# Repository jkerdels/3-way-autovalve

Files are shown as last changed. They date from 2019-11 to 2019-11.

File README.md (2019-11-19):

# 3-way-autovalve
A motorized 3-way-valve to automatically supply washing machines with warm or cold water to reduce the electricity needed by the washing machine.

This project contains all the necessary files to build a motorized 3-way-valve that can supply a washing machine with first warm and then cold water during a regular washing program in order to reduce the overall electric energy needed by the washing machine.

The design is based on some underlying constraints:

- no modification of the particular washing machine
- all custom mechanical parts should be printable with a low-end 3D-printer
- parts should be easily repairable
- if something breaks, it should still be possible to operate the valve manually
- all parts used should be off-the-shelf, cheap, and easy to acquire
- programming is done using the arduino platform to keep things simple

As sole sensor the device uses a flow meter to measure the volume of water that is supplied to the washing at multiple points in time during the washing program. Based on that the code running on the arduino estimates at which stage of a typical washing program (main phase + multiple rinses) the washing machine is. It supplies warm water for the main phase and cold water for all other phases, and resets automatically when the washing program has reached its end.

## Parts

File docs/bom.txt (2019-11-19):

Bill of materials for this project (a.k.a. the stuff you need):

2x
ball valve with 1/2" threads
example: https://www.amazon.de/gp/product/B00NVGNDTA/ref=ppx_yo_dt_b_asin_title_o03_s00

1x
T-connector with 1/2" threads
example: https://www.amazon.de/gp/product/B00IWX7P96/ref=ppx_yo_dt_b_asin_title_o03_s00

1x
flow sensor with 1/2" threads
example: https://www.amazon.de/gp/product/B079QYRQT5/ref=ppx_yo_dt_b_asin_title_o02_s00

1x
geared motor
example: https://www.amazon.de/gp/product/B0752SM4XG/ref=ppx_yo_dt_b_asin_title_o09_s00

1x
motor driver LM 298
example: https://www.amazon.de/gp/product/B07PVYWCXN/ref=ppx_yo_dt_b_asin_title_o08_s00

1x
arduino-nano
example: https://www.amazon.de/gp/product/B07PYNKSCF/ref=ppx_yo_dt_b_asin_title_o01_s00

1x
voltage regulator
example: https://www.amazon.de/gp/product/B01GJ0SC2C/ref=ppx_yo_dt_b_asin_title_o09_s00

3x
push-buttons
example: https://www.amazon.de/gp/product/B06XCSB9N3/ref=ppx_yo_dt_b_asin_title_o05_s01

2x
ball bearing 6mm x 17mm x 6mm
example: https://www.amazon.de/gp/product/B079NSJZ9G/ref=ppx_yo_dt_b_search_asin_title

plus small amounts of:
- wires
- solder
- one LED + suitable voltage dropping resistor
- zipties
- epoxy
- nuts and bolts
- two springs for the end-stops

access to a 3D-printer to print the parts

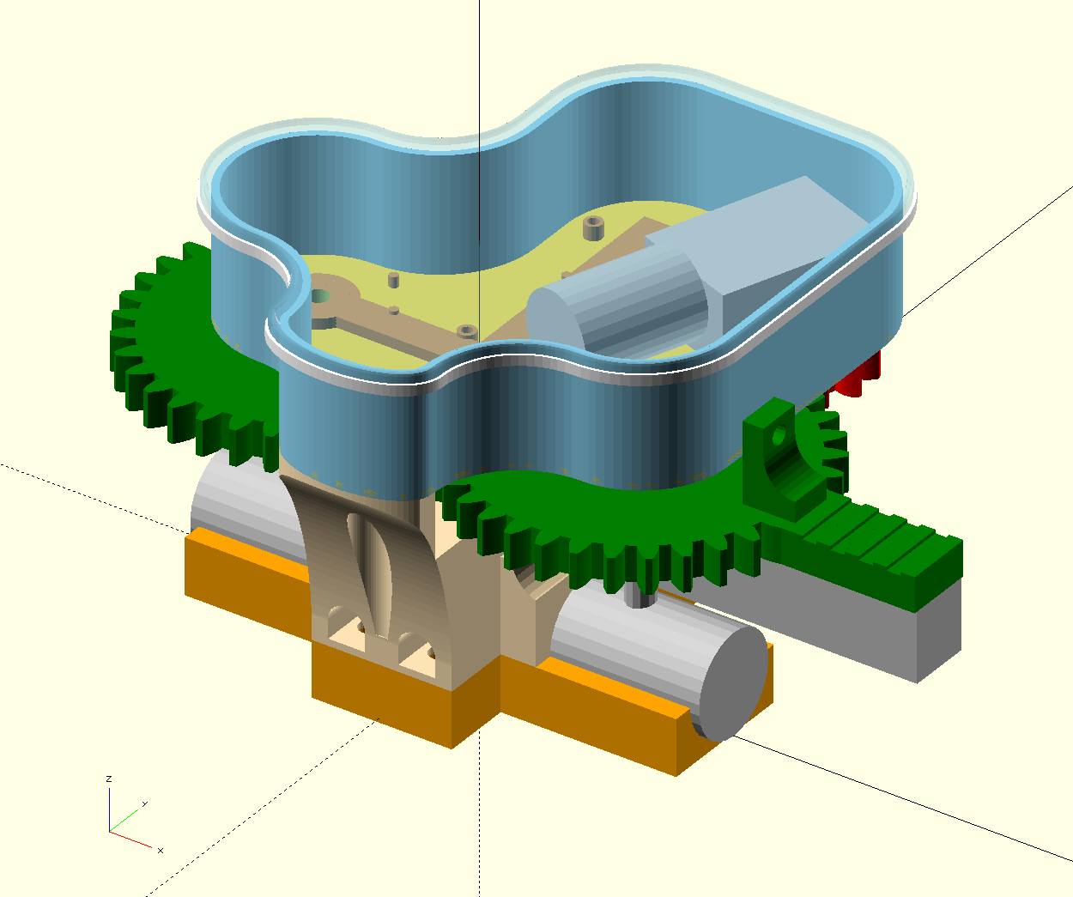
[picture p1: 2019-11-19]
3d-parts/3-way-valve.png

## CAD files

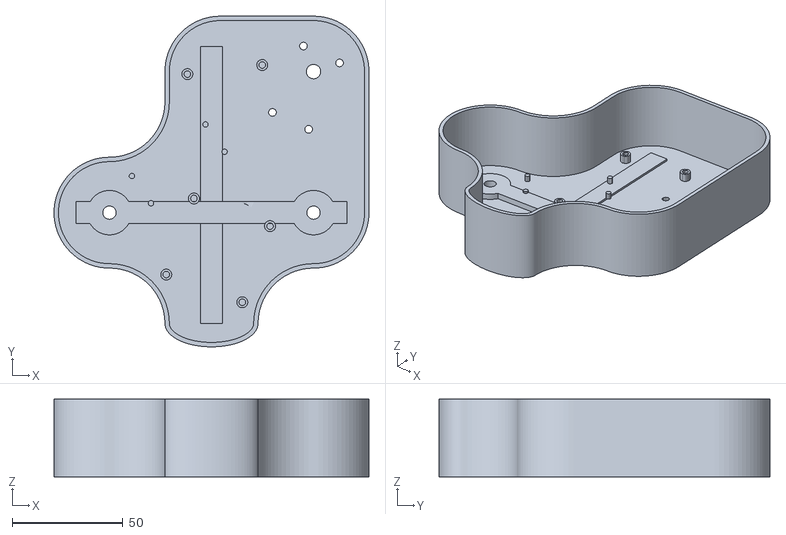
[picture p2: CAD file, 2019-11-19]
3d-parts/stl/top_case.stl
142.0 x 149.1 x 35.0

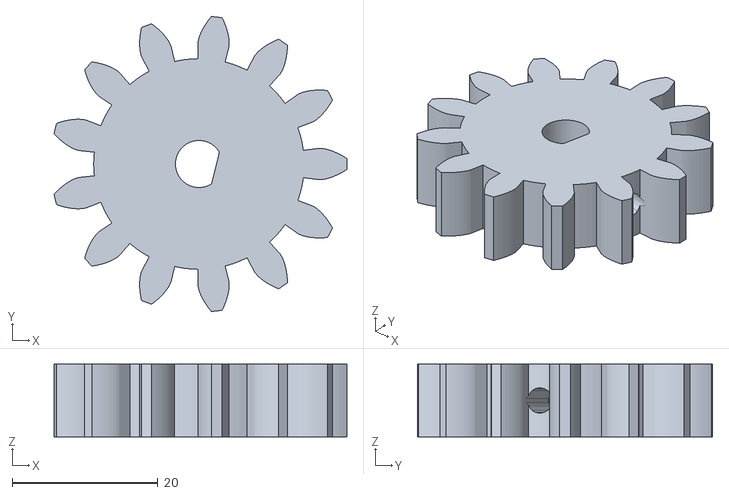
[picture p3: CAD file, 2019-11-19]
3d-parts/stl/drive_gear.stl
40.1 x 40.4 x 10.0

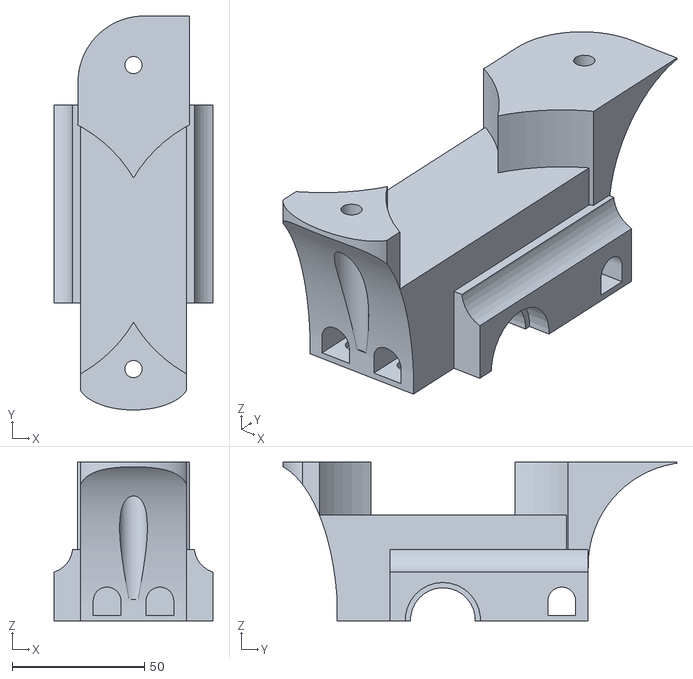
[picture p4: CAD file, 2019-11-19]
3d-parts/stl/holder_stand.stl
60.0 x 149.1 x 60.0

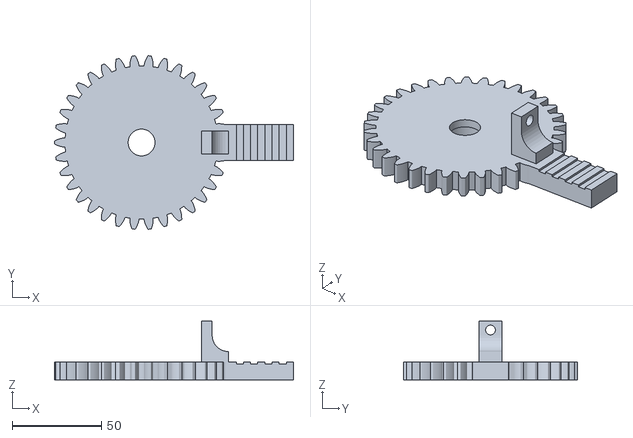
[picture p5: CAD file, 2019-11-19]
3d-parts/stl/lever_gear.stl
133.7 x 97.1 x 32.9

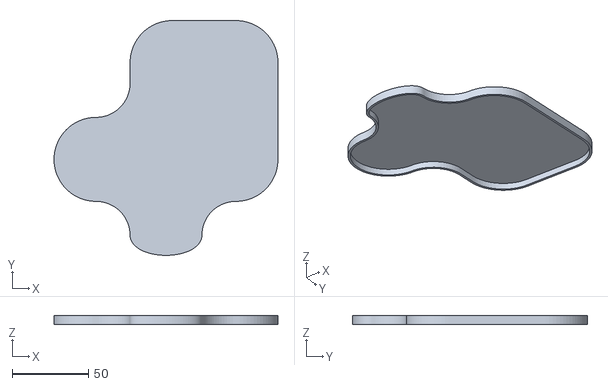
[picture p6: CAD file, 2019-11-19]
3d-parts/stl/top_case_lid.stl
147.2 x 154.3 x 6.00

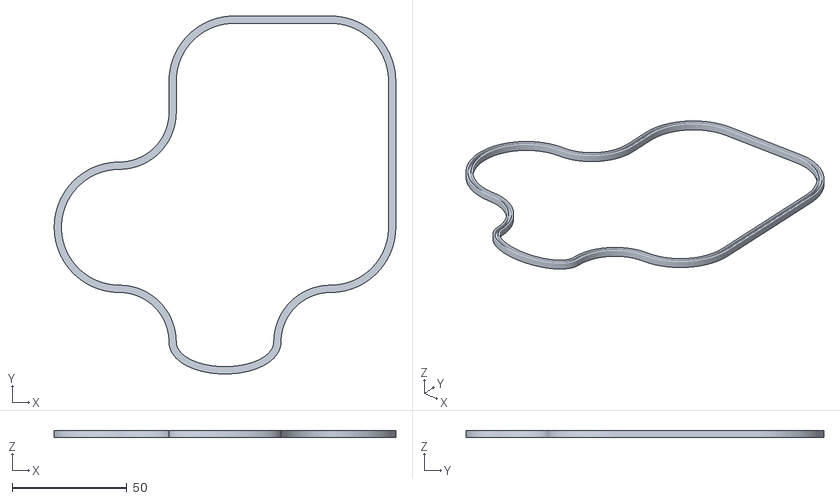
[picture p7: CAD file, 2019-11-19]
3d-parts/stl/top_case_seal.stl
148.8 x 155.9 x 3.00

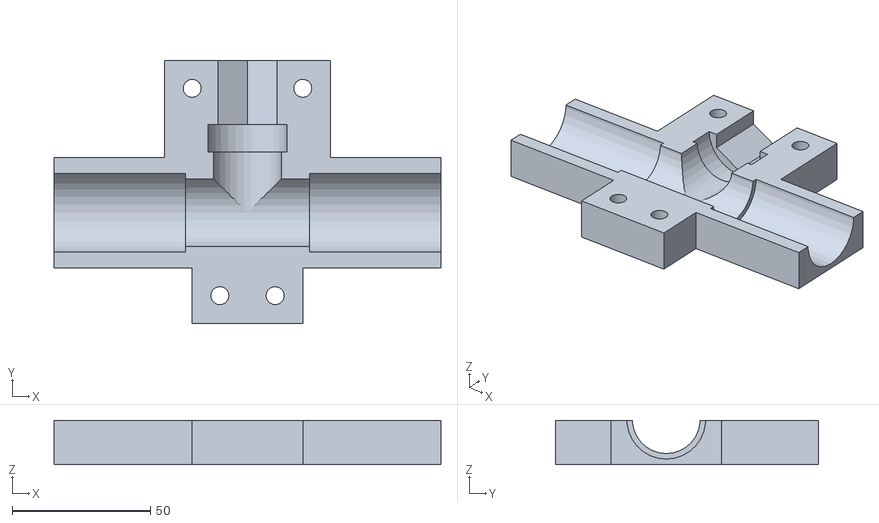
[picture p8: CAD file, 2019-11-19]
3d-parts/stl/holder_base.stl
140.0 x 95.0 x 16.0

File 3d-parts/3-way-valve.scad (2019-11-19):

// for the gears we use the Getriebe.scad library
// https://www.thingiverse.com/thing:1604369
use <Getriebe.scad>;

// to export/print any part, make the just_<part> variable true
// and re-render the model
just_case         = false;
just_case_lid     = false;
just_lever_gear   = false;
just_drive_gear   = false;
just_motor        = false;
just_piping       = false;
just_etronics     = false;
just_holder_base  = false;
just_holder_stand = false;
just_case_seal    = false;

// Distance between the axis of the two opposing valves.
// This value depends on the valves and the T-pipe between
// them that you choose for your version of the 3-way-valve
valve_axis_distance = 92;

// nr of teeth you want on the main gears
nr_of_gearteeth     = 34;
// nr of teeth you want on the gear attached to the motor
drive_gear_teeth    = 13;

// diameter of the "round parts" of the top case that houses
// the motor and the electronics
case_outer_diam     = 50;

// height of the top case
case_outer_height   = 35;

// height of the gears. You can increase this height to
// reduce the load on each gear tooth, e.g., when your
// valves are very hard to move
gear_height         = 10;

// the gap between gears and top case
gear_case_spacing = 4;

// depending on your 3d-printer, holes may be printed too
// small (or too big). With this parameter you can tweak
// the size of all holes to meet the characteristics of
// your printer. 
hole_extra  = 0.5;

// this function just checks if any of the above "just_*" variables is true
function show_all() = !just_case && !just_case_lid && !just_lever_gear && !just_drive_gear && !just_motor && !just_piping && !just_etronics && !just_holder_base && !just_holder_stand && !just_case_seal;

// from here on it is just a series of modules that
// describe the geometry
module piping() {

sp = 24+hole_extra;
lp = 28+hole_extra;

translate([valve_axis_distance/2,0,lp/2])
cylinder(d=8,h=50-lp/2);

translate([-valve_axis_distance/2,0,lp/2])
cylinder(d=8,h=50-lp/2);

translate([-45/2,0,sp/2+2])
rotate([0,90,0])
cylinder(d=sp,h=45);

translate([0,24,sp/2+2])
rotate([90,0,0])
cylinder(d=sp,h=24);

translate([45/2,0,lp/2])
rotate([0,90,0])
cylinder(d=lp,h=50);

translate([-45/2-50,0,lp/2])
rotate([0,90,0])
cylinder(d=lp,h=50);

translate([0,8+24,lp/2])
rotate([90,0,0])
cylinder(d=lp,h=10);

translate([0,30+24+8,sp/2+2])
rotate([90,0,0])
rotate([0,0,30])
cylinder(d=sp,h=30,$fn=6);

translate([valve_axis_distance/2-10,-9,40])
cube([95,18,20]);

translate([-valve_axis_distance/2+9,0,40])
rotate([0,0,90])
translate([-10,0,0])
cube([95,18,20]);

translate([-13,32,20])
cube([3,30,10]);

}

module end_stop() {
    difference(){
        union(){
            cube([15,13,15]);
            translate([0,0,15])
            cube([6,13,8]);
        }

        translate([15,-1,15])
        rotate([-90,0,0])
        cylinder(d=18,h=15,$fn=36);

        translate([-1,13/2,18])
        rotate([0,90,0])
        cylinder(d=5+hole_extra,h=8,$fn=18);
    }
}

module lever_gear(){
    difference(){
        stirnrad(m,nr_of_gearteeth,gear_height,14.5+hole_extra,optimiert=false);
        cylinder(d=17+hole_extra,h=6,$fn=72);
    }
    translate([25,-10,0])
    difference(){
        cube([60,20,10]);
        translate([52,-1,9])
        cube([4,22,3]);
        translate([44,-1,9])
        cube([4,22,3]);
        translate([36,-1,9])
        cube([4,22,3]);
        translate([28,-1,9])
        cube([4,22,3]);
    }
    translate([case_outer_diam/2+8.5,-13/2,gear_height-0.1])
    end_stop();
}

module motor(diff_helper = false) {
    gearbox_width  = 32;
    gearbox_length = 46.1;
    gearbox_height = 21.1;
    
    translate([-14,-gearbox_width/2,-(gearbox_height+2)])
    union(){
        cube([gearbox_length,gearbox_width,gearbox_height]);
        translate([14,gearbox_width/2,gearbox_height-1])
        cylinder(h=3,d=14.5,$fn=36);
        translate([14,gearbox_width/2,gearbox_height-1])
        cylinder(h=14+3,d=6+hole_extra,$fn=36);
        translate([5.5,7,gearbox_height-1]) {
            cylinder(h=3,d=8,$fn=18);
            if (diff_helper) {
                cylinder(h=20,d=3+hole_extra,$fn=18);
            }
        }
        translate([5.5,gearbox_width-7,gearbox_height-1]) {
            cylinder(h=3,d=8,$fn=18);
            if (diff_helper) {
                cylinder(h=20,d=3+hole_extra,$fn=18);
            }
        }
        translate([38.5,7,gearbox_height-1]) {
            cylinder(h=3,d=8,$fn=18);
            if (diff_helper) {
                cylinder(h=20,d=3+hole_extra,$fn=18);
            }
        }
        translate([38.5,gearbox_width-7,gearbox_height-1]) {
            cylinder(h=3,d=8,$fn=18);
            if (diff_helper) {
                cylinder(h=20,d=3+hole_extra,$fn=18);
            }
        }
        translate([gearbox_length,6+24.5/2,24.5/2-4])
        rotate([0,90,0])
        cylinder(d=24.5,h=35);
    }
}

if (show_all()) {
    color("Silver")
    translate([valve_axis_distance/2,valve_axis_distance/2+drive_gear_diam/2,60+gear_height+gear_case_spacing+2.1])
    rotate([180,0,-110])
    motor();
} else if (just_motor) {
    motor();
}

if (show_all()) {
    color("Silver")
    piping();
} else if (just_piping) {
    piping();
}

m = valve_axis_distance/nr_of_gearteeth;

if (show_all()) {
    color("Green")
    render()
    translate([valve_axis_distance/2,0,60]) 
    lever_gear();

    color("Green")
    render()
    translate([-valve_axis_distance/2,0,60])
    rotate([0,0,90])
    lever_gear();
} else if (just_lever_gear) {
    lever_gear();
}

drive_gear_diam = m * drive_gear_teeth;

module drive_gear() {
    gd = 5.95;
    cap = 5.3;
    
    teeth_angle = 360/drive_gear_teeth;
    render()
    difference(){
        union(){
            stirnrad(m,drive_gear_teeth,gear_height,gd+hole_extra,optimiert=false);
            rotate([0,0,-teeth_angle/2])
            translate([gd/2-(gd-cap),-3,0])
            cube([3,6,gear_height]);
        }
        rotate([0,0,-teeth_angle/2])
        translate([0,0,gear_height/2])
        rotate([0,90,0])
        cylinder(d=3+hole_extra,h=30,$fn=18);
    }
}

color("Red")
if (show_all()) {
    translate([valve_axis_distance/2,0,0])
    rotate([0,0,0])
    translate([0,valve_axis_distance/2+drive_gear_diam/2,60])
    rotate([0,0,20])
    drive_gear();
} else if (just_drive_gear) {
    drive_gear();
}

module case_shape(case_diam) {

difference(){
union() {
    translate([valve_axis_distance/2,0])
    circle(d=case_diam,$fn=72);

    translate([valve_axis_distance/2,valve_axis_distance/2+drive_gear_diam/2])
    circle(d=case_diam,$fn=72);

    translate([-(valve_axis_distance-2*case_diam)/2,valve_axis_distance/2+drive_gear_diam/2])
    circle(d=case_diam,$fn=72);

    translate([0,-case_diam])
    scale([1,0.5])
    circle(d=valve_axis_distance-case_diam,$fn=72);

    translate([-valve_axis_distance/2,0])
    circle(d=case_diam,$fn=72);

    translate([-valve_axis_distance/2,-case_diam])
    square([valve_axis_distance,2*case_diam]);

    translate([valve_axis_distance/2-1,0])
    square([case_diam/2+1,valve_axis_distance/2+drive_gear_diam/2]);

    translate([-(valve_axis_distance-2*case_diam)/2,valve_axis_distance/2+drive_gear_diam/2-1])
    square([valve_axis_distance-case_diam,case_diam/2+1]);

    translate([-(valve_axis_distance-2*case_diam)/2-case_diam/2,valve_axis_distance/2+drive_gear_diam/2-1-case_diam/2])
    square([valve_axis_distance-case_diam+case_diam/2,case_diam/2+1]);

}

translate([-valve_axis_distance/2,-case_diam])
circle(d=case_diam,$fn=72);

translate([valve_axis_distance/2,-case_diam])
circle(d=case_diam,$fn=72);

translate([-valve_axis_distance/2,case_diam])
circle(d=case_diam,$fn=72);
}

}



module case(case_diam,case_height,floor_thickness,wall_thickness) {

difference(){    
    union(){
        linear_extrude(height=floor_thickness)
        case_shape(case_diam);

        color("Peru")
        translate([-(valve_axis_distance/2),0,0])
        cylinder(d=20,h=5,$fn=72);

        color("Peru")
        translate([(valve_axis_distance/2),0,0])
        cylinder(d=20,h=5,$fn=72);
        
        color("Peru")
        translate([-(valve_axis_distance/2)-15,-5,0])
        cube([valve_axis_distance+30,10,5]);

        color("Peru")
        translate([-5,-50,0])
        cube([10,125,3]);

        color("Peru")
        translate([6,64.5,floor_thickness])
        rotate([0,0,35])
        power_reg(true);
        
        color("Peru")
        translate([3,-17,floor_thickness])
        rotate([0,0,-20])
        motor_driver(true);

        color("Peru")
        translate([-15,22,floor_thickness])
        rotate([0,0,35])
        arduino_nano(true);    

    }
        translate([-(valve_axis_distance/2),0,-1])
        cylinder(d=6,h=15,$fn=36);
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

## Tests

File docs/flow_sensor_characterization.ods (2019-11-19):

ticks per 10 liter | accumulated time (ms) between ticks | ml per tick | flow (l/min) | avg. time (ms) between ticks |  | x | X^2 |  |  |  |  | 1 | 0.820252056384578 | 1.21913744953923 | 122
5947 | 44281 | 1.69 | 13.55 | 7.5 | 4.43786982248521 | 7.5 | 56.25 | -0.002117671447776 | 0.604550677140733 | 0.21781905069162 | #N/A | 2 | 1.41844971918198 | 1.40999005671727 | 141
6072 | 48046 | 1.65 | 12.49 | 8 | 4.84848484848485 | 8 | 64 | 0.000198251685515 | 0.01975341702154 | 0.380006459543591 | #N/A | 3 | 2.01241203908384 | 1.49074838638203 | 150
5874 | 68709 | 1.71 | 8.74 | 11.7 | 6.8421052631579 | 11.7 | 136.89 | 0.997544145434107 | 0.559595268040768 | #N/A | #N/A | 4 | 2.60213901609014 | 1.53719688889267 | 154
6035 | 78074 | 1.66 | 7.69 | 13 | 7.83132530120482 | 13 | 169 | 3452.61700507306 | 17 | #N/A | #N/A | 5 | 3.1876306502009 | 1.56856315824573 | 157
5907 | 93415 | 1.7 | 6.43 | 15.9 | 9.35294117647059 | 15.9 | 252.81 | 2162.35237555744 | 5.32349668823151 | #N/A | #N/A | 6 | 3.7688869414161 | 1.59198195468968 | 160
5764 | 105244 | 1.74 | 5.71 | 18.3 | 10.5172413793103 | 18.3 | 334.89 | #N/A | #N/A | #N/A | #N/A | 7 | 4.34590788973575 | 1.61071062194685 | 162
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

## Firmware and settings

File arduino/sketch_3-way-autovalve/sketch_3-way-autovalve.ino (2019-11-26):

//-------------------------------------------------------------------------
// pin configuration

// There are three color-coded buttons in the top-case lid and
// one LED. The buttons are wired such that they close to GND
// when pushed. The LED is wired in series with a suitable resistor
// and is driven directly by one IO pin
const int blue_button_pin  = 11;
const int red_button_pin   = 10;
const int green_button_pin = 12;
const int green_led_pin    = 9;

// the flow meter uses a hall-effect sensor and returns one pulse
// per given amount of water volume (sorta, see calibration table below)
const int flow_meter_pin = 5;

// the motor is driven by an LM 298. So we need the typical in1, in2, and
// enable pins
const int motor_en_A = A3;
const int motor_in_1 = A4;
const int motor_in_2 = A5;

// the two endstops are wired as "close to GND" and indicate whether the
// blue (cold) or red (hot) water valve is closed
const int blue_closed_pin = 3;
const int red_closed_pin  = 4;

// end of pin configuration
//-------------------------------------------------------------------------

// this lookup-table allows to measure the amount of water flowing through
// the flow sensor per sensor tick depending on the time between two ticks,
// i.e., depending on how fast the water is flowing. The values represent
// 100th milliliter per tick, e.g., the first value in the array represents
// 1.22 ml per tick. The array is indexed with the time between two ticks
// measured in milliseconds. If the time between two ticks is longer than
// 100 milliseconds, the last value in the array is used.
// The array was derived by measuring the sensor output for a fixed amount
// of water with different flow rates and then fitting a quadratic 
// polynomial to the resulting values. Given t as time in milliseconds the
// full equation to derive the lookup table is: 
// 100*t / (-0.002117671*t^2 + 0.604550677*t + 0.217819051)

const byte flow_lookup[101] = {
0,122,141,150,154,157,160,162,163,165,166,167,168,169,170,171,172,173,173,
  174,175,176,177,177,178,179,180,181,181,182,183,184,184,185,186,187,188,
  188,189,190,191,192,193,193,194,195,196,197,198,198,199,200,201,202,203,
  204,205,206,206,207,208,209,210,211,212,213,214,215,216,217,218,219,220,
  221,222,223,224,226,227,228,229,230,231,232,233,235,236,237,238,239,241,
  242,243,244,246,247,248,250,251,252,254
};

//-------------------------------------------------------------------------
// parameters for auto mode

// these parameters control the heuristic that drives the opening and closing
// of the valves depending on the volume of water used by the washing machine
// and the time past after certain events

// What is the minimum amount of water that has to flow in the beginning
// to be recognized as the water filling of the main phase of the washing program
const unsigned long min_main_flow_volume     = 700000ul; // 7 liters (in hundreds of milliliters)

// What is the minimum time that has to pass after the most recent flow of
// water has come to a stop to recognize the end of water filling of the main phase
const unsigned long min_main_after_flow_time = 240000ul; // 4 minutes (in milliseconds)

// What is the minimum amount of water that has to flow to be recognized as 
// the water filling of a rinse phase of the washing program
const unsigned long min_rinse_flow_volume     = 1000000ul; // 10 liters (in hundreds of milliliters)

// What is the minimum time that has to pass after the most recent flow of
// water has come to a stop to recognize the end of water filling of a rinse phase
const unsigned long min_rinse_after_flow_time = 240000ul; // 4 minutes (in milliseconds)

// The program measures the time of the first rinse phase to identify all subsequent
// rinse phases. What is the amount of time to wait after that measured time span to
// identify the end of the washing program, i.e., how long to wait after the last
// rinse phase to come to the conclusion that the program has ended and we should
// reset to the beginning to be ready for the next load of laundry
const unsigned long rinse_duration_buffer = 180000ul; // 3 minutes (in milliseconds)

// end of parameters for auto mode
//-------------------------------------------------------------------------

// arduino setup routine to initialize all the bells and whistles
void setup() {
  // setting up the buttons
  pinMode(blue_button_pin ,   INPUT_PULLUP);
  pinMode(red_button_pin  ,   INPUT_PULLUP);
  pinMode(green_button_pin,   INPUT_PULLUP);
  pinMode(green_led_pin,      OUTPUT);
  digitalWrite(green_led_pin, LOW);

  // setting up the flow meter input
  pinMode(flow_meter_pin, INPUT);

  // setting up motor output
  pinMode(motor_in_1, OUTPUT);
  digitalWrite(motor_in_1, LOW);

  pinMode(motor_in_2, OUTPUT);
  digitalWrite(motor_in_2, LOW);

  pinMode(motor_en_A, OUTPUT);
  digitalWrite(motor_en_A, LOW);

  // setting up endstops
  pinMode(blue_closed_pin, INPUT_PULLUP);
  pinMode(red_closed_pin , INPUT_PULLUP);  

  // debug
  Serial.begin(115200);
}

// this variable holds the accumulated flow of the
// water flow sensor in 100th of ml
unsigned long accumulated_flow = 0;
byte water_is_flowing = 0;

// variables to control the global state
const byte PS_auto             = 0;
const byte PS_auto_wait        = 5;
const byte PS_manual_red       = 10;
const byte PS_manual_red_wait  = 15;
const byte PS_manual_blue      = 20;
const byte PS_manual_blue_wait = 25;
const byte PS_manual_motor_off = 29;
const byte PS_all_stop         = 30;

const byte PS_idle             = 40;
const byte PS_delay            = 50;
const byte PS_delay_wait       = 55;

byte program_state = PS_all_stop;

byte valve_return = PS_all_stop;

// state parameters
unsigned int PS_delay_duration;

bool expecting_first_flow = false;
unsigned long last_flow_stop      = 0;
unsigned long phase_start         = 0;
unsigned long last_phase_duration = 0;

// since this is a potentially long running application we need to take care
// of the millis() timer coming around after hitting its maximum value. This
// takes place after around 49 days of operation. To avoid this, we modulo
// the time with 2^31 (i.e., "AND" it with 2^31-1) and shift the current time 
// value temporarily in the upper half of our data type when we calculate time 
// spans between "now" and some earlier point in time (see safe_time_delta() 
// function).

// global time
unsigned long now = 0;
// global time modulus
const unsigned long now_mod = 0x80000000; // 2^31
const unsigned long now_and = 0x7FFFFFFF; // 2^31 - 1

inline unsigned long safe_time_delta(const unsigned long now, const unsigned long earlier) {
  return ((now + now_mod) - earlier) & now_and;
}

// main program loop (repeated externally)
void loop() {
  // set global time for this iteration
  now = millis() & now_and;
  // do things
  button_inputs();
  flow_meter_input();
  process_program_state();
}

//--------------------------------------------------------------------------------
// if you want to add or modify functionality of the buttons just add the code in
// the following event functions (button_pressed / button_released). See the
// button_inputs() method to understand when these events are triggered. This method
// already takes care of debouncing the buttons btw.

// button event processing
const byte BS_NONE  = 0;
const byte BS_BLUE  = 1;
const byte BS_RED   = 2;
const byte BS_GREEN = 4;

// the "button_states" byte contains information about the
// states of the other buttons using the bit-positions
// defined above
void blue_pressed(const byte button_states) {
  program_state = PS_manual_blue;
  valve_return  = PS_idle;
  digitalWrite(green_led_pin, LOW);
  /*
  Serial.print("blue_pressed, states: ");
  Serial.println(button_states, BIN);
  */
}

// "press_duration" is the time in ms of how long the button was pressed
void blue_released(const byte button_states, const unsigned int press_duration) {
  /*
  Serial.print("blue_released, states: ");
  Serial.print(button_states, BIN);  
  Serial.print(", duration: ");
  Serial.println(press_duration, DEC);
  */
}

void red_pressed(const byte button_states) {
  program_state = PS_manual_red;
  valve_return  = PS_idle;
  digitalWrite(green_led_pin, LOW);
  /*
  Serial.print("red_pressed, states: ");
  Serial.println(button_states, BIN);
  */
}

void red_released(const byte button_states, const unsigned int press_duration) {
  /*
  Serial.print("red_released, states: ");
  Serial.print(button_states, BIN);  
  Serial.print(", duration: ");
  Serial.println(press_duration, DEC);  
  */
}

void green_pressed(const byte button_states) {
  /*
  Serial.print("green_pressed, states: ");
  Serial.println(button_states, BIN);
  */
}

void green_released(const byte button_states, const unsigned int press_duration) {
  if (press_duration < 2500) {
    program_state = PS_auto;
  }
  // TODO: create a learning mode entered by holding down the green button for
  // more than 2.5 seconds in which the system learns the different phases of
  // a washing program via manual user input while the washing program is running.
  /*
  Serial.print("green_released, states: ");
  Serial.print(button_states, BIN);  
  Serial.print(", duration: ");
  Serial.println(press_duration, DEC);    
  */
}

//--------------------------------------------------------------------------------
// flow events

// if you want to add or modify what happens when a new flow of water is detected
// or its end, just change these event methods. See flow_meter_input() function
// to understand when these events are triggered. The total accumulated flow
// measured by the sensor is available through the global variable "accumulated_flow"

void new_flow_started() {  
  Serial.println("flow started");
  if (expecting_first_flow) {
    expecting_first_flow  = false;
    last_flow_stop        = now;
    last_phase_duration   = safe_time_delta(now,phase_start);
    phase_start           = now;
  }
}

void flow_stopped(const unsigned long flow_time, const unsigned long flow_volume) {
  
  Serial.print("flow ended, time: ");
  Serial.print(flow_time, DEC);    
  Serial.print(", volume: ");
  Serial.println(flow_volume, DEC);    

  last_flow_stop = now;
}

//--------------------------------------------------------------------------------
// handle program state

// this method controls the overal behavior of the automatic valve, including
// states that deal with manual operation of the valves triggered by pressing
// the red or blue buttons, and the automatic mode that is entered by pressing
// the green button and indicated by the green LED

void process_program_state() {

  // used by some states to control the flow in the state machine
  // in a more flexible way, e.g., the delay state
  static byte return_state = PS_idle;

  static unsigned long delay_start = 0;

  static unsigned long manual_start = 0;

  // washing machine states
  const byte EMS_INIT            = 0;
  const byte EMS_START           = 10;
  const byte EMS_MAIN_FILL       = 20;
  const byte EMS_MAIN_WASH       = 30;
  const byte EMS_1ST_RINSE_FILL  = 40;
  const byte EMS_1ST_RINSE_WASH  = 50;
  const byte EMS_NTH_RINSE_FILL  = 60;
  const byte EMS_NTH_RINSE_WASH  = 70;

  static byte est_machine_state = EMS_INIT;

  static unsigned long rinse_wash_start = 0;
  static unsigned long rinse_duration   = 0;
  

  switch (program_state) {

    case PS_auto : {
      Serial.println("entered automatic mode");
      motor_stop();
      // switch on green light
      digitalWrite(green_led_pin, HIGH);
      // initialize estimated machine state
      est_machine_state = EMS_INIT;
      phase_start       = now;
      Serial.println("opening hot water valve...");        
      valve_return = PS_auto_wait;
      program_state = PS_manual_red;
      
    } break;

    case PS_auto_wait : {
      switch (est_machine_state) {
        
        case EMS_INIT : {
          Serial.println("waiting for initial flow...");  
          expecting_first_flow = true;
          accumulated_flow     = 0;    
          est_machine_state = EMS_START;
        } break;
        
        case EMS_START : {
          // wait for first flow to occur
          if (expecting_first_flow == false) {
            Serial.println("main fill started");
            est_machine_state = EMS_MAIN_FILL;
          }
        } break;

        case EMS_MAIN_FILL : {
          // wait for end of flow by waiting for at least
          // [min_main_flow_volume] liters of water and [min_main_after_flow_time] after last flow stop
          if ((water_is_flowing == 0) && 
              (accumulated_flow > min_main_flow_volume) && 
              (safe_time_delta(now,last_flow_stop) > min_main_after_flow_time))
          {
            // switch from hot to cold water and wait for rinse
            valve_return         = PS_auto_wait;
            program_state        = PS_manual_blue;
            est_machine_state    = EMS_MAIN_WASH;
            expecting_first_flow = true;
            accumulated_flow     = 0;
            Serial.println("Assuming to be in main wash. Switching to cold water and waiting for 1st rinse fill.");
          }
        } break;

        case EMS_MAIN_WASH : {
          // wait for first rinse flow to occur
          if (expecting_first_flow == false) {
            Serial.print("Main phase took ");
            Serial.print(last_phase_duration / 60000ul);
            Serial.println(" minutes.");
            Serial.println("First rinse fill started.");
            est_machine_state = EMS_1ST_RINSE_FILL;
          }
        } break;

        case EMS_1ST_RINSE_FILL : {
          // wait for end of flow by waiting for at least
          // [min_rinse_flow_volume] liters of water and [min_rinse_after_flow_time] after last flow stop
          if ((water_is_flowing == 0) && 
              (accumulated_flow > min_rinse_flow_volume) && 
              (safe_time_delta(now,last_flow_stop) > min_rinse_after_flow_time))
          {
            // wait for 2nd rinse
            est_machine_state    = EMS_1ST_RINSE_WASH;
            expecting_first_flow = true;
            accumulated_flow     = 0;
            Serial.println("Assuming to be in 1st rinse wash. Waiting for 2nd rinse fill.");
          }
        } break;

        case EMS_1ST_RINSE_WASH : {
          // wait for second rinse flow to occur
          if (expecting_first_flow == false) {
            rinse_duration   = last_phase_duration;
            rinse_wash_start = now;
            Serial.print("1st rinse phase took ");
            Serial.print(last_phase_duration / 60000ul);
            Serial.println(" minutes.");
            Serial.println("Second rinse fill started.");
            est_machine_state = EMS_NTH_RINSE_FILL;
          }
        } break;

        case EMS_NTH_RINSE_FILL : {
          // wait for end of flow by waiting for at least
          // [min_rinse_flow_volume] liters of water and [min_rinse_after_flow_time] after last flow stop
          if ((water_is_flowing == 0) && 
              (accumulated_flow > min_rinse_flow_volume) && 
              (safe_time_delta(now,last_flow_stop) > min_rinse_after_flow_time))
          {
            // wait for rinse to stop or a further rinse to start
            est_machine_state    = EMS_NTH_RINSE_WASH;
            expecting_first_flow = true;
            accumulated_flow     = 0;
            Serial.println("Assuming to be in a rinse wash. Waiting for it to end or a further rinse fill to start.");
          }
        } break;

        case EMS_NTH_RINSE_WASH : {
          // wait for a further rinse flow to occur
          if (expecting_first_flow == false) {
            rinse_duration = last_phase_duration;
            rinse_wash_start = now;
            Serial.print("the last rinse phase took ");
            Serial.print(last_phase_duration / 60000ul);
            Serial.println(" minutes.");
            Serial.println("Another rinse fill started.");
            est_machine_state = EMS_NTH_RINSE_FILL;
          } else
          if (safe_time_delta(now,rinse_wash_start) > (rinse_duration + rinse_duration_buffer)) {
            // no further rinse appears to happen, assume we are done
            Serial.println("Assuming end of program. Returning to start.");
            program_state = PS_auto;
          }
          
        } break;

      }
    } break;

    
    case PS_manual_red : {
      motor_forward();
      manual_start = now;
      program_state = PS_manual_red_wait;
    } break;

    case PS_manual_red_wait : {
      if ((digitalRead(blue_closed_pin) == LOW) || (safe_time_delta(now,manual_start) > 4800)) {
        PS_delay_duration = 200;
        return_state = PS_manual_motor_off;
        program_state = PS_delay;
      }
    } break;

    case PS_manual_blue : {
      motor_backward();
      manual_start = now;
      program_state = PS_manual_blue_wait;
    } break;

    case PS_manual_blue_wait : {
      if ((digitalRead(red_closed_pin) == LOW) || (safe_time_delta(now,manual_start) > 4800)) {
        PS_delay_duration = 200;
        return_state = PS_manual_motor_off;
        program_state = PS_delay;
      }      
    } break;

    case PS_manual_motor_off : {
      motor_stop();
      program_state = valve_return;      
    } break;

    // depricated state
    case PS_all_stop : {
      motor_stop();
      program_state = PS_idle;
    } break;

    case PS_idle : {
      
    } break;

    case PS_delay : {
      delay_start = now;
      program_state = PS_delay_wait;
    } break;

    case PS_delay_wait : {
      if (safe_time_delta(now,delay_start) > PS_delay_duration) {
        program_state = return_state;
      }
    } break;

  }
  
}

//------------------------------------------------------------------------------
//------------------------------------------------------------------------------
//------------------------------------------------------------------------------
// below here are "only" service functions that do not need to be edited to
// specify the behavior of the system

// read buttons and cause button event functions to be called
void button_inputs() {

  // static time variables for debouncing
  static unsigned long blue_push_time  = 0;
  static unsigned long red_push_time   = 0;
  static unsigned long green_push_time = 0;
 
  const byte debounce_interval = 50;
  
  // static button state
  static byte button_states = BS_NONE;

  // check for button press events and store time
  if (((button_states & BS_BLUE) == 0) && (digitalRead(blue_button_pin) == LOW)) {
    button_states |= BS_BLUE;
    blue_push_time = now;
    blue_pressed(button_states);
  }

  if (((button_states & BS_RED) == 0) && (digitalRead(red_button_pin) == LOW)) {
    button_states |= BS_RED;
    red_push_time = now;
    red_pressed(button_states);
  }

  if (((button_states & BS_GREEN) == 0) && (digitalRead(green_button_pin) == LOW)) {
    button_states |= BS_GREEN;
    green_push_time = now;
    green_pressed(button_states);
  }

  if (((button_states & BS_BLUE) > 0) && (digitalRead(blue_button_pin) == HIGH)) {
    unsigned long down_time = safe_time_delta(now,blue_push_time);
    if (down_time > debounce_interval) {
      button_states &= ~BS_BLUE;
      blue_released(button_states,(const unsigned int)down_time);
    }
  }

  if (((button_states & BS_RED) > 0) && (digitalRead(red_button_pin) == HIGH)) {
    unsigned long down_time = safe_time_delta(now,red_push_time);
    if (down_time > debounce_interval) {
      button_states &= ~BS_RED;
      red_released(button_states,(const unsigned int)down_time);
    }
  }

  if (((button_states & BS_GREEN) > 0) && (digitalRead(green_button_pin) == HIGH)) {
    unsigned long down_time = safe_time_delta(now,green_push_time);
    if (down_time > debounce_interval) {
      button_states &= ~BS_GREEN;    
      green_released(button_states,(const unsigned int)down_time);
    }
  }  
}


void flow_meter_input() {

  static unsigned long flow_begin  = 0;
  static unsigned long flow_volume = 0;
  static unsigned long last_flow_time = now;
  static byte last_val = digitalRead(flow_meter_pin);

  unsigned long delta = safe_time_delta(now,last_flow_time);

  if ((water_is_flowing == 20) && (delta > 2000)) {
    // we have not received flow ticks for two seconds
    // so we assume the flow has stopped
    water_is_flowing = 0;
    flow_stopped(safe_time_delta(now,flow_begin) - delta,flow_volume);
  }
  
  int val = digitalRead(flow_meter_pin);
  if ((val != last_val) && (val == HIGH)) {        
    if (delta < 150) {
      unsigned int cur_flow = delta <= 100 ? flow_lookup[delta] : 297;
      accumulated_flow += cur_flow;
      flow_volume      += cur_flow;
      // wait for at least 20 ticks before we announce that a new
      // flow has started
      if (water_is_flowing < 20) {
        if (++water_is_flowing == 20) {
          flow_begin  = now;
          flow_volume = 0;
          new_flow_started();
        }
      }
    } else if (delta > 2000){
      // this is (probably) a new flow, as the
      // last measurement is "long ago" (5 seconds)
      water_is_flowing = 0;
    }
    last_flow_time = now;
  }
  last_val = val;    
}

void motor_forward() {
  motor_stop();
   
  digitalWrite(motor_in_1, LOW);
  digitalWrite(motor_in_2, HIGH);
  
  digitalWrite(motor_en_A, HIGH);
}

void motor_backward() {
  motor_stop();

  digitalWrite(motor_in_1, HIGH);
  digitalWrite(motor_in_2, LOW);
  
  digitalWrite(motor_en_A, HIGH);
}

void motor_stop() {
  digitalWrite(motor_in_1, LOW);
  digitalWrite(motor_in_2, LOW);
  digitalWrite(motor_en_A, LOW);  
}

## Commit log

2019-11-19 added the 3d-parts to the project
    [3-way-valve.scad, drive_gear.stl, holder_base.stl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]
2019-11-19 added arduino code
2019-11-19 added first parts of the documentation
    [30Grad-Vollwaschprogramm-Flow.ods, flow_sensor_characterization.ods]
2019-11-19 added bill of materials
2019-11-19 added time-based fallback in case end-stops fail
    [sketch_3-way-autovalve.ino]
2019-11-21 added data of second testrun with different machine
    [30Grad-Vollwaschprogramm-Flow2.ods]
2019-11-26 fixed a bug in the end of program detection
    [sketch_3-way-autovalve.ino]
